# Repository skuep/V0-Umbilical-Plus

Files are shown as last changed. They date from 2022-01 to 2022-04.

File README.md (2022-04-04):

# Note that this Repo is the 'Plus' Version of the original V0-Umbilical
The original version was created by GitHub user timmit99 and can be found in the official Voron-Hardware repository.

The 'Plus' version of the V0-Umbilical features an integrated ADXL345 Accelerometer that can be used for Input Shaper Tuning.
The Molex MicroFit connector was changed from a 14-pin to 20-pin version to acommodate the additional wires for the ADXL345.

In the following, the changes to the original README from timmit99 is given. Please read the README in the original project first.

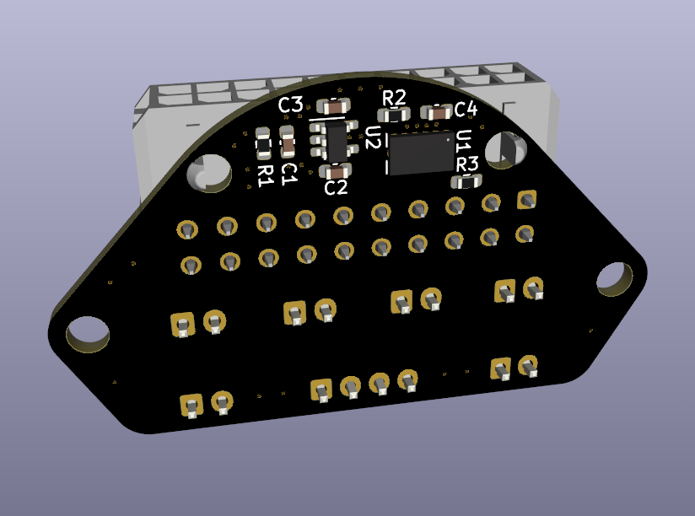
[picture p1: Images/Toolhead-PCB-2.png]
Toolhead PCB with ADXL345 Accelerometer
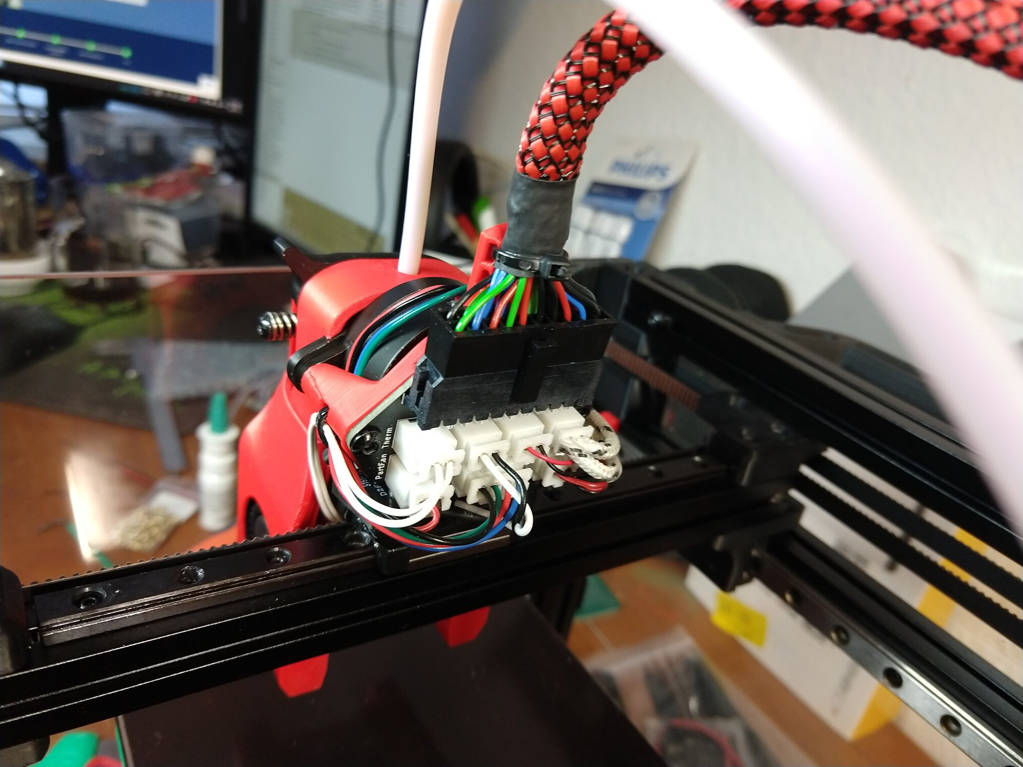
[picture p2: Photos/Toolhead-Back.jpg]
Photograph of Toolhead with mounted Umbilical PLUS
 | 
|:---:|:---:|

### Frame PCB BOM
| Part | Quantity | Notes | LCSC Part Number | Link |
| --- | :-: | --- | --- |--- |
| 20 Pin Socket |  1 | MOLEX 430452012 | C485575 | https://www.lcsc.com/product-detail/Wire-To-Board-Wire-To-Wire-Connector_MOLEX-430452012_C485575.html |
| SMD Thermistor  |  1 | 100K 0805 Thermistor | C143680 | https://lcsc.com/product-detail/NTC-Thermistors_Vishay-Intertech-NTCS0805E3104FXT_C143680.html |
| 2 pin JST XH |  5 | 2.5mm pitch | C158012 | https://lcsc.com/product-detail/Wire-To-Board-Wire-To-Wire-Connector_JST-Sales-America-B2B-XH-A-LF-SN_C158012.html |
| 3 pin JST XH |  2 | 2.5mm pitch | C144394 | https://lcsc.com/product-detail/Wire-To-Board-Wire-To-Wire-Connector_JST-Sales-America-B3B-XH-A-LF-SN_C144394.html |
| 4 pin JST XH |  3 | 2.5mm pitch | C144395 | https://lcsc.com/product-detail/Wire-To-Board-Wire-To-Wire-Connector_JST-Sales-America-B4B-XH-A-LF-SN_C144395.html |
| 6 pin JST XH |  1 | 2.5mm pitch | C144397 | https://www.lcsc.com/product-detail/Wire-To-Board-Wire-To-Wire-Connector_JST-Sales-America_B6B-XH-A-LF-SN_JST-Sales-America-B6B-XH-A-LF-SN_C144397.html |
| Screw Terminal  |  1 | 5.08mm pitch | C8465 | https://lcsc.com/product-detail/Screw-terminal_Ningbo-Kangnex-Elec-WJ500V-5-08-2P_C8465.html |

### Optional Parts
| Part | Quantity | Notes | LCSC Part Number | Link |
| --- | :-: | --- | --- |--- |
| 0805 10uF Capacitor  |  3 | Use if using BARE neopixel IC's. Strips have these already. | C17024 | https://lcsc.com/product-detail/Multilayer-Ceramic-Capacitors-MLCC-SMD-SMT_Samsung-Electro-Mechanics-CL21A106KPFNNNE_C17024.html |
----

### Toolhead PCB BOM
| Part | Quantity | Notes | LCSC Part Number | Link |
| --- | :-: | --- | --- |--- |
| 20 Pin Socket (Right Angle) | 1 |  Molex 430452000  | C485576 | https://www.lcsc.com/product-detail/Wire-To-Board-Wire-To-Wire-Connector_MOLEX-430452000_C485576.html |
| 2 pin JST XH | 6 |  B2B-XH  | C158012 | https://lcsc.com/product-detail/Wire-To-Board-Wire-To-Wire-Connector_JST-Sales-America-B2B-XH-A-LF-SN_C158012.html |
| 4 pin JST XH | 1 |  B4B-XH  | C144395 | https://lcsc.com/product-detail/Wire-To-Board-Wire-To-Wire-Connector_JST-Sales-America-B4B-XH-A-LF-SN_C144395.html |
| LP2985-33DBVR | 1 | 3.3V LDO | C95414 | https://www.lcsc.com/product-detail/Linear-Voltage-Regulators-LDO_Texas-Instruments-LP2985-33DBVR_C95414.html |
| ADXL345BCCZ | 1 | Accelerometer | C9667 | https://www.lcsc.com/product-detail/Motion-Sensors-Accelerometers_Analog-Devices-ADXL345BCCZ-RL7_C9667.html |
| 10 Ohm Resistor | 2 | 0603 size |  C22859  | https://www.lcsc.com/product-detail/Chip-Resistor-Surface-Mount_UNI-ROYAL-Uniroyal-Elec-0603WAF100JT5E_C22859.html |
| 10 kOhm Resistor| 1 | 0603 size | C25804 | https://www.lcsc.com/product-detail/Chip-Resistor-Surface-Mount_UNI-ROYAL-Uniroyal-Elec-0603WAF1002T5E_C25804.html |
| 4.7uF Capacitor | 2 | 0603 size |  C19666  | https://www.lcsc.com/product-detail/Multilayer-Ceramic-Capacitors-MLCC-SMD-SMT_Samsung-Electro-Mechanics-CL10A475KO8NNNC_C19666.html |
| 10nF Capacitor  | 2 | 0603 size |  C57112  | https://lcsc.com/product-detail/Multilayer-Ceramic-Capacitors-MLCC-SMD-SMT_10nF-103-10-50V_C57112.html/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 |
---

Corresponding CPL and BOM files are included in the repository. Using these files you can easily get yourself a ready-made assembled PCB from JLCPCB so you don't have to have the skills to solder the fine-pitch and 0603 packages.

## Umbilical cable

The Umbilical cable is a 220-240mm dual ended 20P (2x10) microfit cable. The connectors are wired 1:1 so pin 1 connects to pin 1 and so forth for all 20 pins.

### Cable BOM
| Part | Quantity | Notes | LCSC Part Number | Link |
| --- | :-: | --- | --- |--- |
| 20 Pin Plug | 2  | Molex 430252000 | C485324 | https://lcsc.com/product-detail/Connectors-Housings_MOLEX-430252000_C485324.html |
| Crimps 20 AWG | 12 | Molex 430300001/430300007 | C259786 | https://lcsc.com/product-detail/Line-Pressing-Terminals_MOLEX-430300001_C259786.html |
| Crimps 26 AWG | 28 | Molex 430300004/430300010 | C259765 | https://lcsc.com/product-detail/Line-Pressing-Terminals_MOLEX-430300004_C259765.html |
| 20AWG Wire | 6  | 220mm Sections  | | PTFE/Silicone/Hefulon for motion rated, PVC *could* work since it isn't constraind to a cable chain |
| 26AWG Wire | 14 | | |  |

MicroFit connectors support two different ranges of conductor thickness using different wire crimp ferrules. I recommend that you realize the stepper motor and heater wires with 20AWG wire (0.5mm²) and the remaining wires in 26AWG wire (0.14mm²) to save on weight and accelerated mass.

## Hints and Remarks
### Extruder Stepper Direction
The umbilical cable reverses the stepper rotation direction. I.e. you need to invert the DIR pin of the extruder motor in your printer.cfg file.

    [extruder]
    ....
    dir_pin: PB4 # Add ! (or remove ! if already there) before 'PB4'
    ....

### Mounting the Toolhead PCB
The umbilical toolhead PCB uses heat stake inserts in order to mount it to the motor screws. In some cases (i.e. LDO motors), the extruder motor already has an additional thread, which has to be either removed by drilling the motor holes with a 3mm spiral drill. If you do not want to drill into the motor, you can use M3x10 captive screws, which are unfortunately hard to find. These screws have a narrowed section and a short thread at the tip so they only 'grab' the thread of the heat stake inserts.

### Additional chamber thermistor on SKR mini V2.0
If you are using the SKR mini V2.0 board and you want to connect the chamber thermistor, you can use Timmit99's expansion board (https://github.com/VoronDesign/Voron-Hardware/tree/master/SKR-Mini_TFT_Thermistor_Board). 

If you want an easier and faster solution, you can move the Z-STOP endswitch pin and connect it the E0-STOP pin using a simple self-made JST 2-pin to 3-pin adapter (See Photos folder) or by removing the crimp pins from the 2-pin JST and insert them into the housing of a 3-pin JST header. Once the Z-STOP pin is freed up, you can use it for your thermistor. This method needs the following printer.cfg changes:

    [stepper_z]
    ...
    endstop_pin: ^PC15 # Conversion for additional thermistor (use E0-STOP for Z-STOP)
    ...
    
    [temperature_sensor chamber]
    sensor_type: Generic 3950
    sensor_pin: PC2
    gcode_id: C
    pullup_resistor: 10000

### Connecting the ADXL345 to a Raspberry Pi
The ADXL345 circuit on the toolhead PCB includes a R-C filter and a 3.3V low-dropout regulator to deliver a clean power supply. Thus you can use the official drawings shown in the corresponding docs (https://www.klipper3d.org/Measuring_Resonances.html), with one small change. You need to connect VCC to +5V (Pin 2 or Pin 4) instead of 3.3V (Pin 1) on the Raspberry Pi extension header (See Photos folder). Then follow the official docs for setting the resonance measurement up.

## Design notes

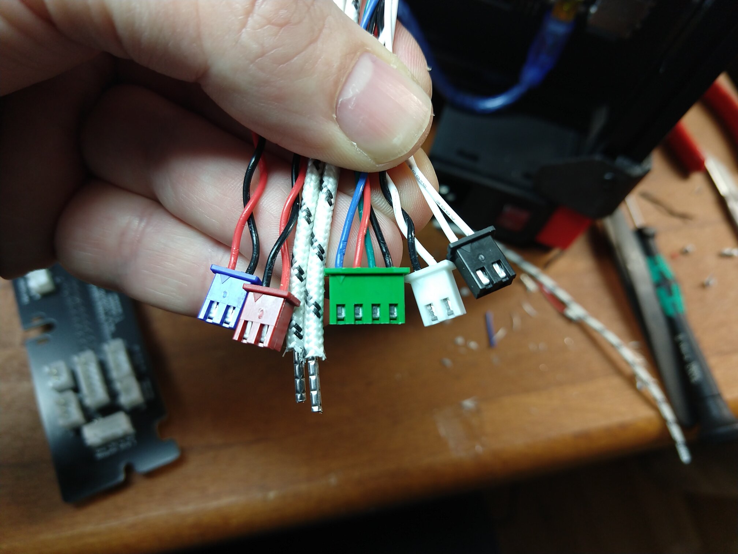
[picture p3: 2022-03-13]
Photos/Wires-from-SKR-Controller-Board.jpg

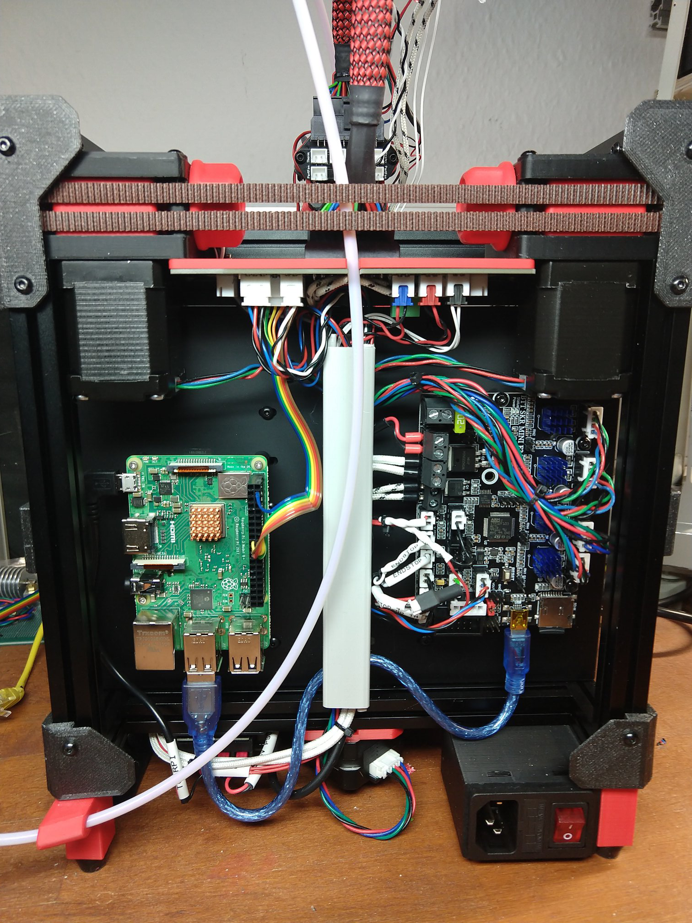
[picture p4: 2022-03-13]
Photos/Back-Panel-Closed.jpg

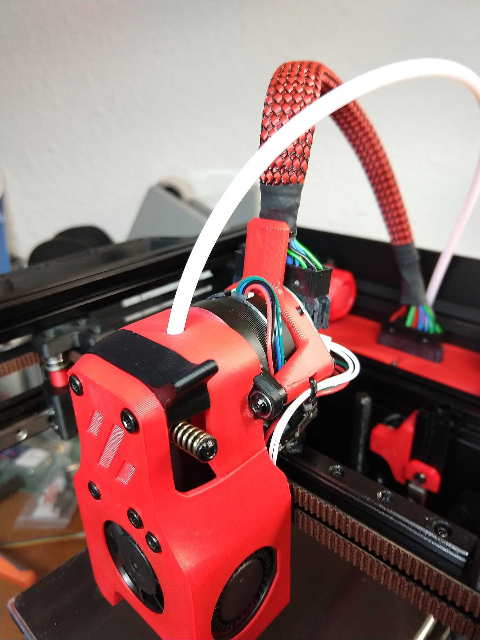
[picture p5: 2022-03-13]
Photos/Toolhead-Front.jpg

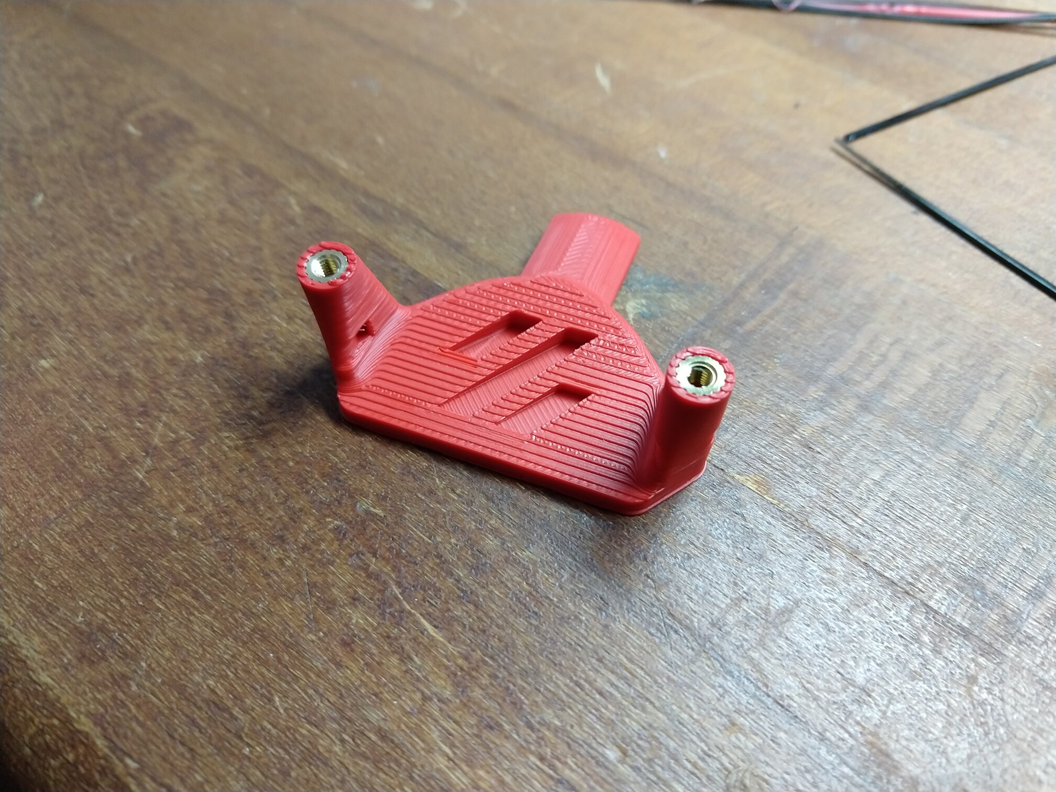
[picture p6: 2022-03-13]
Photos/Toolhead-Mount-Top.jpg

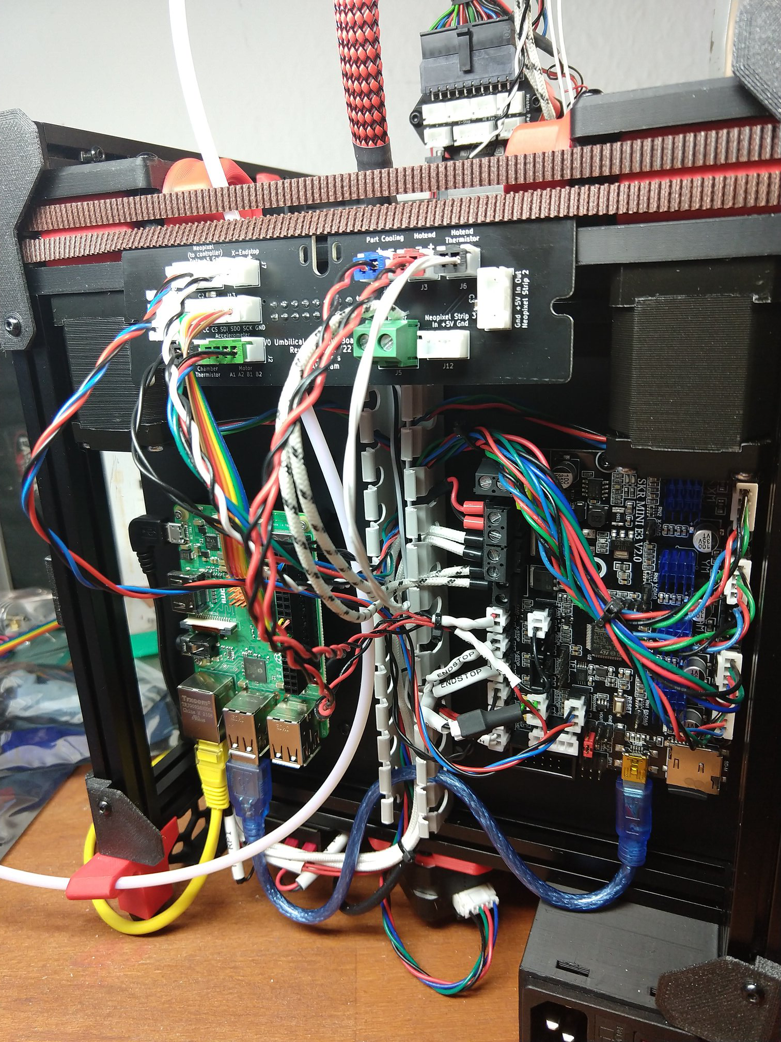
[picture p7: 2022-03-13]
Photos/Back-Panel-Open.jpg

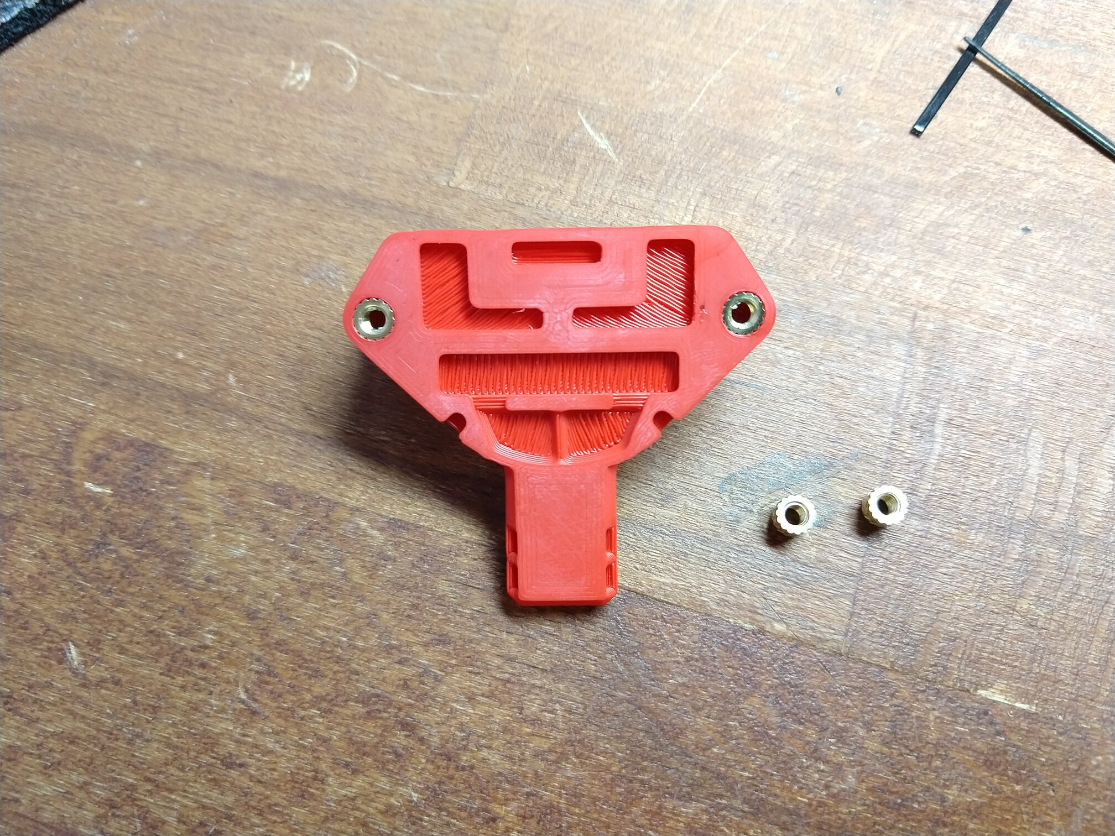
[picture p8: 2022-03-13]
Photos/Toolhead-Mount-Bottom.jpg

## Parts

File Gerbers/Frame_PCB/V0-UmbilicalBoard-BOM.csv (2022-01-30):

Id | Designator | Package | Quantity | Designation | Supplier and ref
1 | J1 | Molex_Micro-Fit_3.0_43045-2012_2x10_P3.00mm_Vertical | 1 | Conn_02x10_Top_Bottom
2 | TH1 | R_0805_2012Metric_Pad1.20x1.40mm_HandSolder | 1 | Thermistor
3 | J3 | JST_XH_B2B-XH-A_1x02_P2.50mm_Vertical | 1 | Hotend Fan
4 | J4 | JST_XH_B2B-XH-A_1x02_P2.50mm_Vertical | 1 | Part Cooling Fan
5 | J6 | JST_XH_B2B-XH-A_1x02_P2.50mm_Vertical | 1 | Thermistor
6 | J7 | JST_XH_B2B-XH-A_1x02_P2.50mm_Vertical | 1 | X-Endstop
7 | J8 | JST_XH_B2B-XH-A_1x02_P2.50mm_Vertical | 1 | Chamber Thermistor
8 | J2 | JST_XH_B4B-XH-A_1x04_P2.50mm_Vertical | 1 | Motor
9 | J5 | TerminalBlock_Phoenix_MKDS-1,5-2-5.08_1x02_P5.08mm_Horizontal | 1 | Heater
10 | J9 | JST_XH_B3B-XH-A_1x03_P2.50mm_Vertical | 1 | Neopixel (from controller)
11 | J10,J11 | JST_XH_B4B-XH-A_1x04_P2.50mm_Vertical | 2 | Neopixel Strip 1
12 | C1,C2,C3 | C_0805_2012Metric_Pad1.18x1.45mm_HandSolder | 3 | C
13 | J12 | JST_XH_B3B-XH-A_1x03_P2.50mm_Vertical | 1 | Neopixel Out
14 | J13 | JST_XH_B6B-XH-A_1x06_P2.50mm_Vertical | 1 | Accelerometer

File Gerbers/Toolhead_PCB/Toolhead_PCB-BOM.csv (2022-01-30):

Id | Designator | Package | Quantity | Designation | Supplier and ref
1 | J1 | Molex_Micro-Fit_3.0_43045-2000_2x10_P3.00mm_Horizontal | 1 | Conn_02x10_Top_Bottom
2 | J7 | JST_XH_B2B-XH-A_1x02_P2.50mm_Vertical | 1 | X-Endstop
3 | J5 | JST_XH_B2B-XH-A_1x02_P2.50mm_Vertical | 1 | Heater
4 | J3 | JST_XH_B2B-XH-A_1x02_P2.50mm_Vertical | 1 | Hotend Fan
5 | J6 | JST_XH_B2B-XH-A_1x02_P2.50mm_Vertical | 1 | Thermistor
6 | J4,J8 | JST_XH_B2B-XH-A_1x02_P2.50mm_Vertical | 2 | Part Cooling Fan
7 | J2 | JST_XH_B4B-XH-A_1x04_P2.50mm_Vertical | 1 | Motor
8 | C3,C1 | C_0603_1608Metric | 2 | 4.7u/16V/X5R
9 | C2,C4 | C_0603_1608Metric | 2 | 10n/NP0
10 | U1 | LGA-14_3x5mm_P0.8mm_LayoutBorder1x6y | 1 | ADXL345BCCZ
11 | R2 | R_0603_1608Metric | 1 | 10K
12 | R1,R3 | R_0603_1608Metric | 2 | 10R
13 | U2 | SOT-23-5 | 1 | LP2985-33DBVR

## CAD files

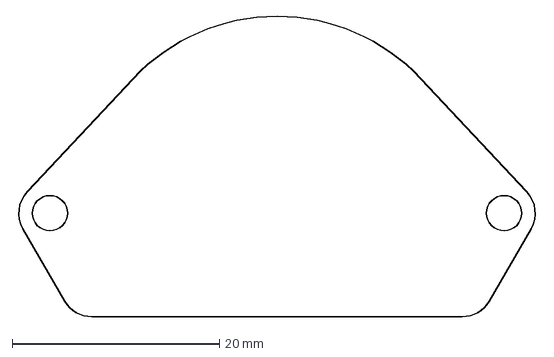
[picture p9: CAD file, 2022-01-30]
CAD/Toolhead_PCB_Outline.DXF
50.4 x 29.0 mm

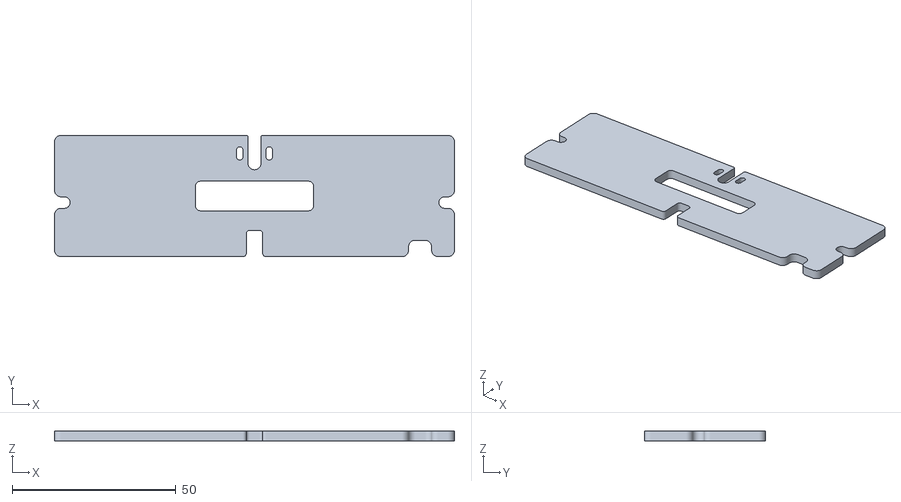
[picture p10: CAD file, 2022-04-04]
STLs/FramePCBCover.stl
122.0 x 37.0 x 3.00

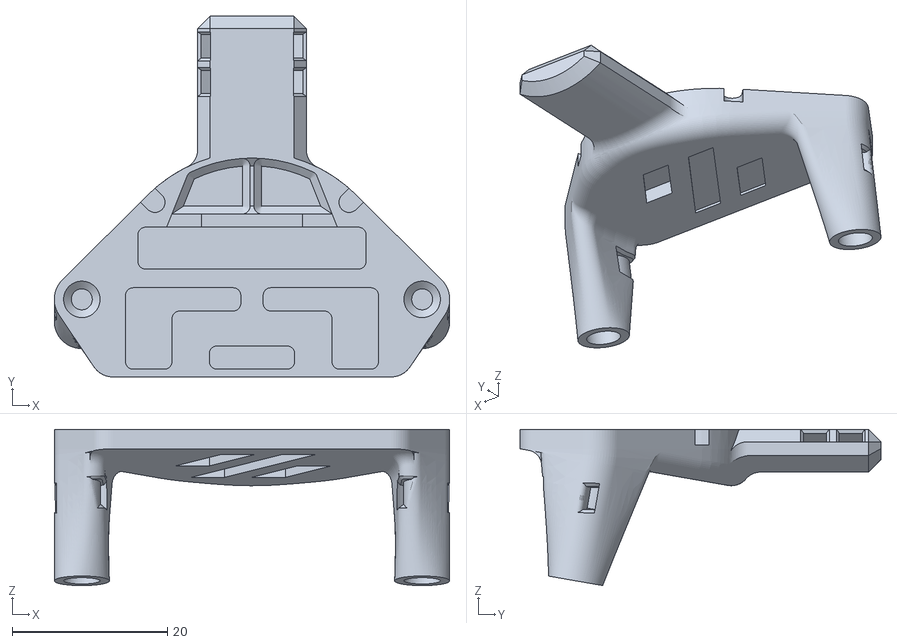
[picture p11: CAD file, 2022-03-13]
STLs/Toolhead-Mount.stl
50.9 x 46.5 x 20.1

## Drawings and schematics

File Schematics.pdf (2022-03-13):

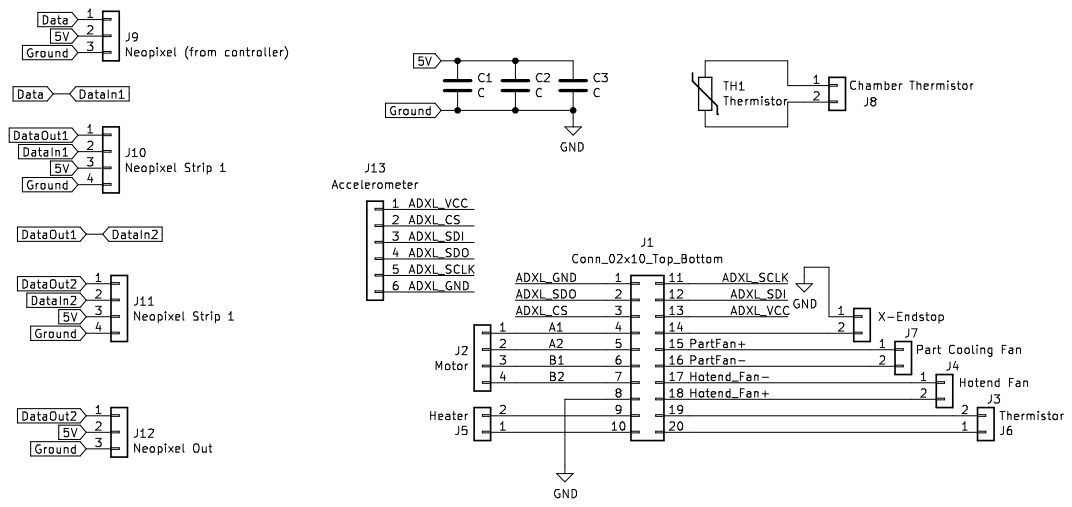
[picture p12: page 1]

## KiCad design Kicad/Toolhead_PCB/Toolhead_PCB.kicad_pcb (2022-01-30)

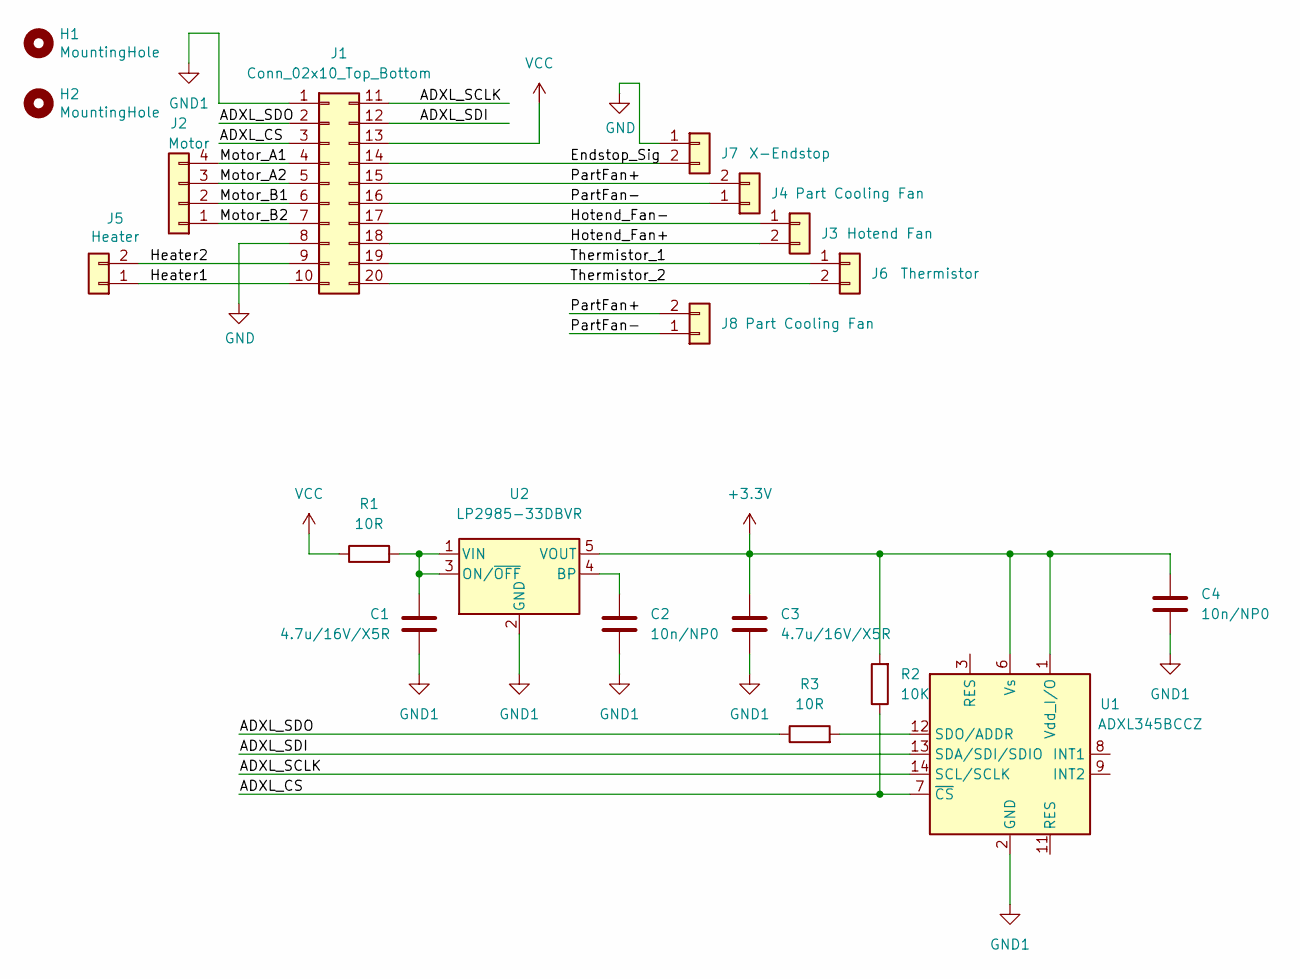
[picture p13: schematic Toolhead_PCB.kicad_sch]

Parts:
C1, C3: 4.7u/16V/X5R; C_0603_1608Metric
C2, C4: 10n/NP0; C_0603_1608Metric
H1, H2: MountingHole; MountingHole_3.2mm_M3
J1: Conn_02x10_Top_Bottom; Molex_Micro-Fit_3.0_43045-2000_2x10_P3.00mm_Horizontal
J2: Motor; JST_XH_B4B-XH-A_1x04_P2.50mm_Vertical
J3: Hotend Fan; JST_XH_B2B-XH-A_1x02_P2.50mm_Vertical
J4, J8: Part Cooling Fan; JST_XH_B2B-XH-A_1x02_P2.50mm_Vertical
J5: Heater; JST_XH_B2B-XH-A_1x02_P2.50mm_Vertical
J6: Thermistor; JST_XH_B2B-XH-A_1x02_P2.50mm_Vertical
J7: X-Endstop; JST_XH_B2B-XH-A_1x02_P2.50mm_Vertical
R1, R3: 10R; R_0603_1608Metric
R2: 10K; R_0603_1608Metric
U1: ADXL345BCCZ; LGA-14_3x5mm_P0.8mm_LayoutBorder1x6y
U2: LP2985-33DBVR; SOT-23-5

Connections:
+3V3: C3.1, C4.1, R2.2, U1.1 (Vdd_I/O), U1.6 (Vs), U2.5 (VOUT)
/ADXL_CS: J1.3, R2.1, U1.7 (~CS)
/ADXL_SCLK: J1.11, U1.14 (SCL/SCLK)
/ADXL_SDI: J1.12, U1.13 (SDA/SDI/SDIO)
/ADXL_SDO: J1.2, R3.1
/Endstop_Sig: J1.14, J7.2
/Heater1: J1.10, J5.1
/Heater2: J1.9, J5.2
/Hotend_Fan+: J1.18, J3.2
/Hotend_Fan-: J1.17, J3.1
/Motor_A1: J1.4, J2.4
/Motor_A2: J1.5, J2.3
/Motor_B1: J1.6, J2.2
/Motor_B2: J1.7, J2.1
/PartFan+: J1.15, J4.2, J8.2
/PartFan-: J1.16, J4.1, J8.1
/Thermistor_1: J1.19, J6.1
/Thermistor_2: J1.20, J6.2
GND: J1.8, J7.1
GND1: C1.2, C2.2, C3.2, C4.2, J1.1, U1.2 (GND), U1.4 (GND), U1.5 (GND), U2.2 (GND)
unnamed: C1.1, R1.2, U2.1 (VIN), U2.3 (ON/~OFF)
unnamed: C2.1, U2.4 (BP)
unnamed: R3.2, U1.12 (SDO/ADDR)
VCC: J1.13, R1.1

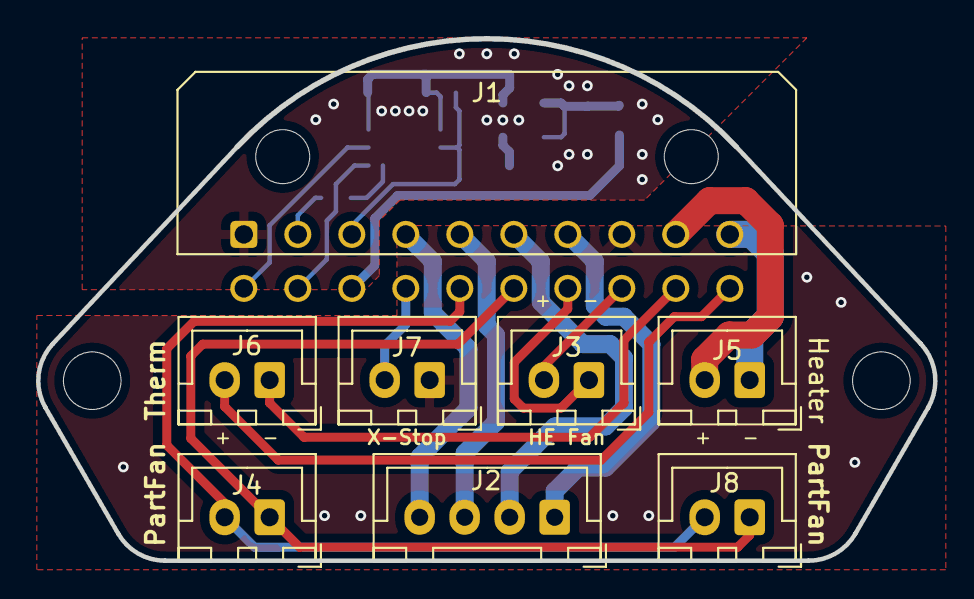
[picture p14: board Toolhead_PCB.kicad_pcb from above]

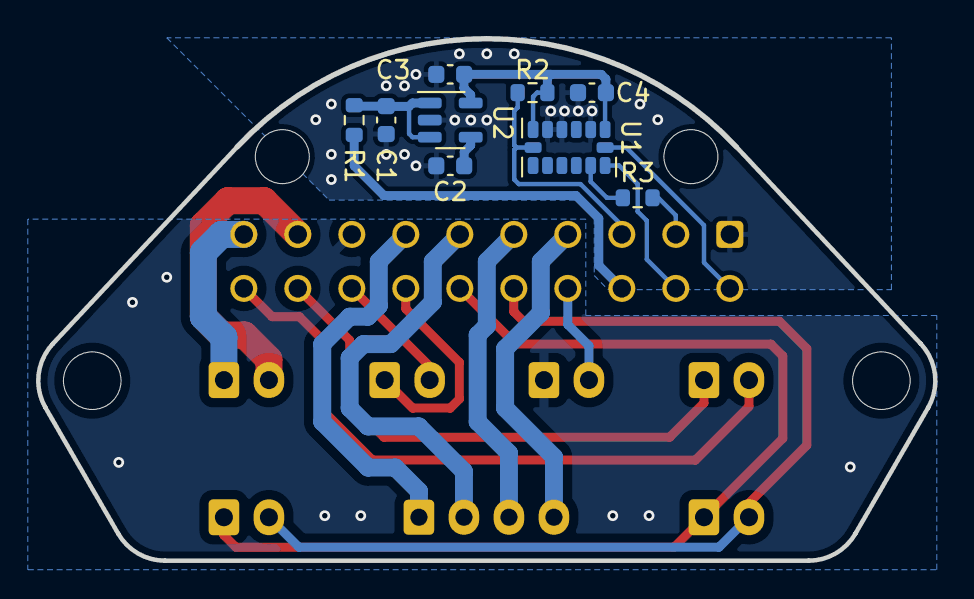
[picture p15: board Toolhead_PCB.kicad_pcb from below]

Board: 2 copper layers, 49.8 x 29.0 mm, 19 parts (9 on the bottom side), 24 nets.

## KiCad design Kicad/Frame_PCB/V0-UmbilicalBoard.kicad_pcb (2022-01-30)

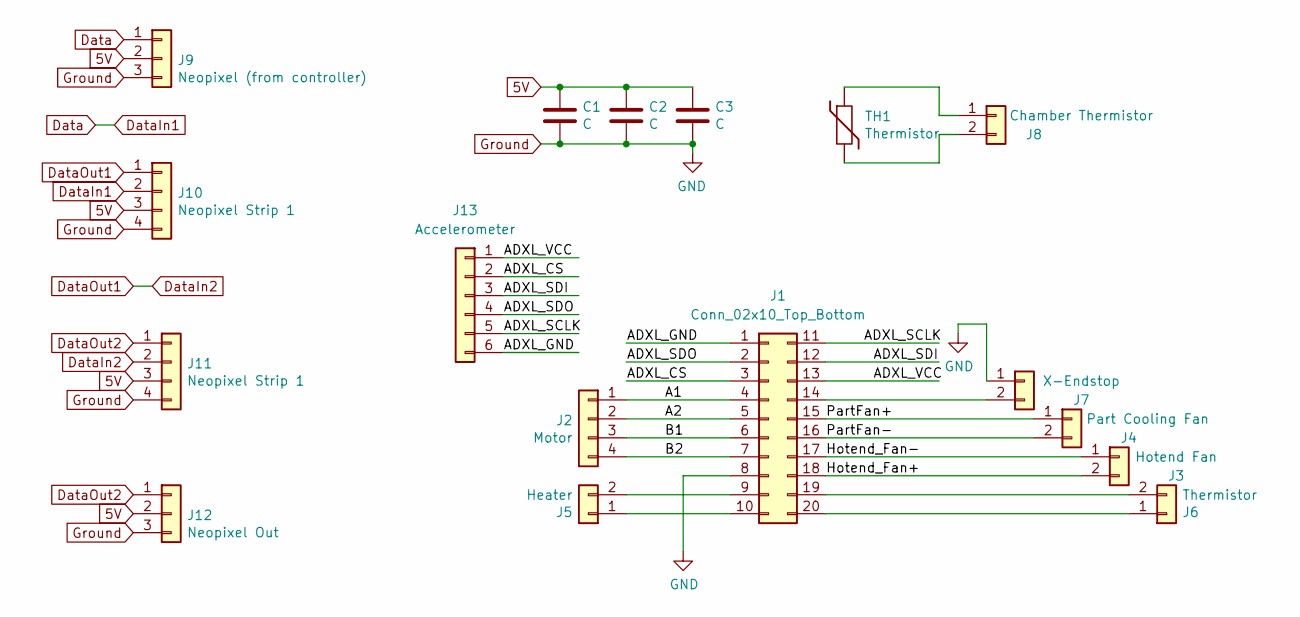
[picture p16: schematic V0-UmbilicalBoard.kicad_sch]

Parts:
C1, C2, C3: C; C_0805_2012Metric_Pad1.18x1.45mm_HandSolder
J1: Conn_02x10_Top_Bottom; Molex_Micro-Fit_3.0_43045-2012_2x10_P3.00mm_Vertical
J2: Motor; JST_XH_B4B-XH-A_1x04_P2.50mm_Vertical
J3: Hotend Fan; JST_XH_B2B-XH-A_1x02_P2.50mm_Vertical
J4: Part Cooling Fan; JST_XH_B2B-XH-A_1x02_P2.50mm_Vertical
J5: Heater; TerminalBlock_Phoenix_MKDS-1,5-2-5.08_1x02_P5.08mm_Horizont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
J6: Thermistor; JST_XH_B2B-XH-A_1x02_P2.50mm_Vertical
J7: X-Endstop; JST_XH_B2B-XH-A_1x02_P2.50mm_Vertical
J8: Chamber Thermistor; JST_XH_B2B-XH-A_1x02_P2.50mm_Vertical
J9: Neopixel (from controller); JST_XH_B3B-XH-A_1x03_P2.50mm_Vertical
J10, J11: Neopixel Strip 1; JST_XH_B4B-XH-A_1x04_P2.50mm_Vertical
J12: Neopixel Out; JST_XH_B3B-XH-A_1x03_P2.50mm_Vertical
J13: Accelerometer; JST_XH_B6B-XH-A_1x06_P2.50mm_Vertical
TH1: Thermistor; R_0805_2012Metric_Pad1.20x1.40mm_HandSolder

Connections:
5V: C1.1, C2.1, C3.1, J9.2, J10.3, J11.3, J12.2
/A1: J1.4, J2.1
/A2: J1.5, J2.2
/ADXL_CS: J1.3, J13.2
/ADXL_GND: J1.1, J13.6
/ADXL_SCLK: J1.11, J13.5
/ADXL_SDI: J1.12, J13.3
/ADXL_SDO: J1.2, J13.4
/ADXL_VCC: J1.13, J13.1
/B1: J1.6, J2.3
/B2: J1.7, J2.4
/Hotend_Fan+: J1.18, J3.2
/Hotend_Fan-: J1.17, J3.1
/PartFan+: J1.15, J4.1
/PartFan-: J1.16, J4.2
Data: J9.1, J10.2
DataIn2: J10.1, J11.2
DataOut2: J11.1, J12.1
Ground: C1.2, C2.2, C3.2, J1.8, J7.1, J9.3, J10.4, J11.4, J12.3
unnamed: J1.9, J5.2
unnamed: J1.10, J5.1
unnamed: J1.14, J7.2
unnamed: J1.19, J6.2
unnamed: J1.20, J6.1
unnamed: J8.1, TH1.1
unnamed: J8.2, TH1.2

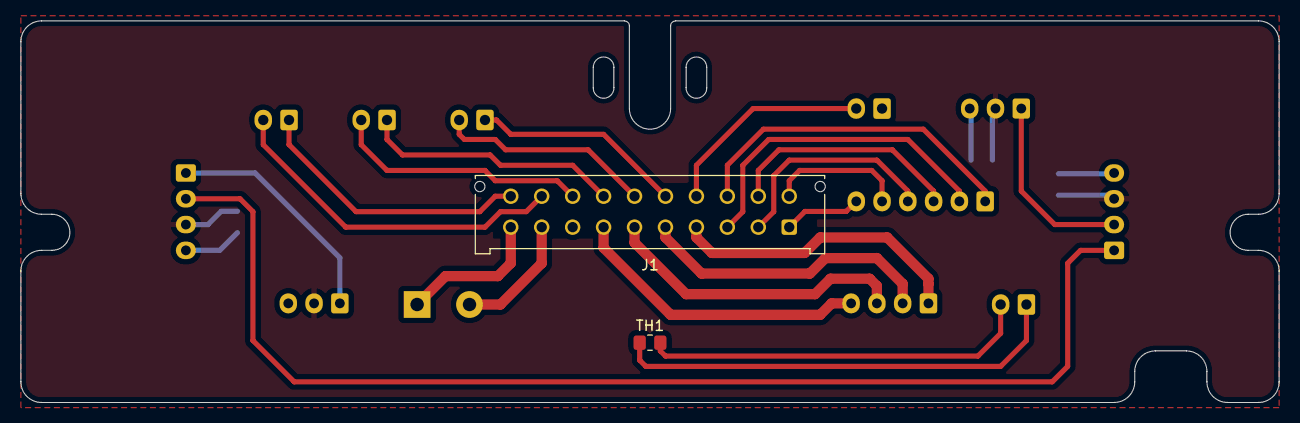
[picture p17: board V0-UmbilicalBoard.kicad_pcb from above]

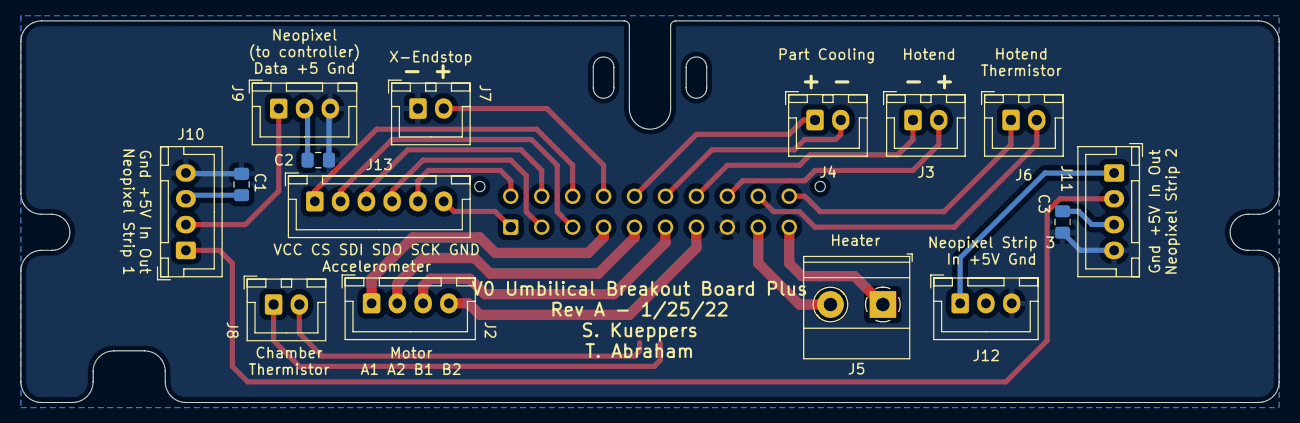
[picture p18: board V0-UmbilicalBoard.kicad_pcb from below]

Board: 2 copper layers, 122.0 x 37.0 mm, 17 parts (15 on the bottom side), 26 nets.

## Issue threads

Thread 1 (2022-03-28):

LP2985-33DBVR Unavailable

allisaurusp, 2022-03-28:
LP2985-33DBVR isn't in stock with JLCPCB. I couldn't find an analogue with the same package, so I'm thinking it would be worth making a revision in favor of a different part or package that's less affected by current shortages.

allisaurusp, 2022-03-28:
XC6206P332MR should be functionally equivalent, and in the same size, but with different pinout. If there are no objections, I'll put together a MR

skuep, 2022-03-29:
Thanks for the hint. It's just dreadful at the moment. I chose the LP2985 because there were still plenty available on the market a few weeks ago. Luckily, this thing has second sources.
In your case, I would choose one of these
https://lcsc.com/product-detail/Linear-Voltage-Regulators-span-style-background-color-ff0-LDO-span_Texas-Instruments-LP2985AIM5X-3-3-NOPB_C271268.html
https://lcsc.com/product-detail/Linear-Voltage-Regulators-span-style-background-color-ff0-LDO-span_Texas-Instruments-LP3985IM5X-3-3-NOPB_C132058.html

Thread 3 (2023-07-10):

Voron V0.2 Tool Head Mount 3D CAD/STL files

fristle, 2023-07-10:
With the upgrade to V0.2 the extruder changed to miniStealthBurner (mSB).
Thus the strain relief body changed, too, and is now a four (4) bolt mount as a structural part of the extruder for more sturdiness.

https://github.com/VoronDesign/Voron-0/tree/Voron0.2r1/STLs/Toolheads/Mini_Stealthburner

Is there a plan or timeline for the Umbilical Plus files being updated to this strain relief?

skuep, 2023-07-10:
Hey there, with everyone moving to various other more popular and more feature rich toolhead PCBs, there is no plan for mini stealthburner compatibility at the moment.

fristle, 2023-07-13:
Thanks for replying so quickly.
I understand the situation.

Anyway, pls find attached a quick'n'dirty 3D design for adding it to the repository.

[Strain_Relief_Body_v0_2_UmbilicalPLUS_Toolhead_x1.zip](https://github.com/skuep/V0-Umbilical-Plus/files/12039519/Strain_Relief_Body_v0_2_UmbilicalPLUS_Toolhead_x1.zip)

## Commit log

2022-01-30 Copy V0-Umbilical to V0-Umbilical-Plus
    [Toolhead_PCB-B_Cu.gbr, Toolhead_PCB-B_Mask.gbr, Toolhead_PCB-B_Paste.gbr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]
2022-01-30 Added accelerometer to Toolhead PCB, modified connector to 20-pin Molex Micro Fit
    [Toolhead_PCB.kicad_pcb, Toolhead_PCB_Outline.DXF]
2022-01-30 Minor changes, added new schematic and project file
    [Toolhead_PCB.kicad_pcb, Toolhead_PCB.kicad_sch]
2022-01-30 Updated Gerber files
    [Toolhead_PCB-B_Cu.gbr, Toolhead_PCB-B_Mask.gbr, Toolhead_PCB-B_Paste.gbr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]
2022-01-30 Added PnP file
    [Toolhead_PCB-all-pos.csv]
2022-01-30 Added BOM file
    [Toolhead_PCB-BOM.csv]
2022-01-30 Updated part number of ICs
    [Toolhead_PCB.kicad_pcb, Toolhead_PCB.kicad_sch]
2022-01-30 Added BOM/CPL file for JLCPCB ordering
    [Toolhead_PCB-JLCPCB-BOM.csv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]
2022-01-30 Changed Micro Fit connector to 20 pin type and added 6-pin XH for accelerometer. Changed silkscreen text
    [V0-UmbilicalBoard.kicad_pcb, V0-UmbilicalBoard.kicad_sch]
2022-01-30 Regenerated gerbers, added PnP and BOM
    [V0-UmbilicalBoard-BOM.csv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]
2022-01-30 Saved Export settings
    [V0-UmbilicalBoard.kicad_pcb]
2022-01-30 Added missing 3D model for Molex MicroFit
    [V0-UmbilicalBoard.kicad_pcb, V0-UmbilicalBoard.kicad_sch]
2022-01-30 Added images of PCBs
2022-01-30 Update README.md
    Added image of Toolhead PCB
2022-01-30 Copy over Frame PCB cover STL
    [FramePCBCover.STL]
2022-03-13 Added Step Models of PCBs
2022-03-13 Added schematics for pinout
2022-03-13 Added STL of 3D printed Toolhead Mount
    [Toolhead-Mount.stl]
2022-03-29 Updated README.md
    Added photograph of toolhead
2022-04-04 Added STL of modified frame PCB cover
    [FramePCBCover.STL, FramePCBCover.stl]
2022-04-04 Fixed wrong number of required wires
2022-04-05 Moved over to the KiCAD JLCPCB plugin
    [BOM-Toolhead_PCB.csv, Toolhead_PCB-JLCPCB-BOM.csv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]
2023-01-02 Added toolhead STL for Mini After LGX Lite
